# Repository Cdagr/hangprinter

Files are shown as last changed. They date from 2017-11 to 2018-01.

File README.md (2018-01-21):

Hangprinter Hangprinter logo
===========

This is the main dev branch of Megaprinter, based off Hangprinter v3.3.
Read [blog](http://vitana.se/opr3d/tbear) to stay up to date with what happens here.

Bill of Materials
----------------

  * Printed parts
    * Beam Clamp x 2
    * Beam Slider x 6
    * Corner Clamp x 3
    * Extruder Holder x 1
    * Lineroller ABC Winch x 3
    * Lineroller D x 3
    * Lineroller Anchor x 6 (The stl contains 2. Print <code>lineroller_anchor.stl</code> 3 times.)
    * Motor Bracket x 4
    * Motor Gear x 4
    * Spool x 4
    * Spool Gear x 4
    * Spacer x 4
    * Cable Clamp x ca 12
  * Vitamins
    * 5 x Nema17 steppers (> 40 N/cm holding torque, flat shaft)
    * 60 m FireLine 0.5 mm
    * ca 47x47 cm MDF or plywood sheet
    * 1 x Arduino Mega
    * 1 x RAMPS
    * 5 x drivers (Special configuration options exist if you use Mechaduinos or tmc2130SilentStepSticks)
    * 1 x USB cable, type B plug
    * 15x15 mm wooden beams (Tobben/core team uses lengths 3x40 cm + 1x20 cm)
    * 1 x Power supply (12 V, 10 A recommended)
    * 13 x M3 screws, length 25 mm
    * 16 x M3 screws, length 5 mm
    * 2  x M3 screws, length 10 mm
    * 4  x M8 screws, length > 50 mm, head countersunk
    * 8  x 608 bearing
    * 12 x 623 V-groove bearing
    * 10 cm PTFE tube (standard bowden, 4 mm outer dia, >1.75 mm inner dia)
    * More than 20 self tapping wooden screws, length 10 - 20 mm, width ca 4 mm
    * 5 m of 15-lead ribbon wire
    * Nuts and washers for all screws
    * Extruder + hot end (any setup that fits Nema17 mount will work)
    * Mechaduino optional addon
      * 4 x Mechaduino PCB
      * More than 20 jumper wires (if Mechaduinos)
      * 5V->3V3 level converter for i2c usage (if Mechaduinos)
    * Tmc2130SilentStepStick addon
      * A few more jumper wires

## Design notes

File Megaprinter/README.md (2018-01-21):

Hangprinter Hangprinter logo
===========

This is for a portable hangprinter tailored for exhibitions in large spaces.
Uses NEMA 23 stepper motors because of larger parts/higher inertia. Beefier motors helps avoid skipped steps w/ open loop control.
Designed in Fusion 360 because I'm not very good at openscad, but later things will be uploaded in openscad when things become more final.

Bill of Materials - Sorry, using hardware standard to US in early versions because they are easier for me to source. Metric to come!
----------------

  * Printed parts - Please print from ABS or other plastic with ~100C temperature resistance
    * Hopper/Fan Mount x 1
    * Bottle Mount x 1
  * Vitamins
    * 1 x NEMA23 stepper motor, 186 oz/in of greater
    * 1 x NEMA23 motor mounting bracket
    * 1 x 1/2in copper or aluminum pipe
    * 3 x 10-32 x 1.5in socket head cap screws
    * 3 x 4-40 x 1/8in set screws
    * 4 x 10-32 x 1/2in set screw
    * 3 x 10-32 x 1/2in countersunk screw
    * 4 x 8-32 x 3/4in socket head cap screws
    * 4 x 8-32 nylock nuts
    * 1/2in wood augur drill bit
    * 3 x heater cartridges, I use 24V 80W
    * 1 x motor coupler 1/4in to 5/16in
    * 1 x 40mm cooling fan, I use a server fan
  * Machined parts
    * Aluminum
      * Heat sink x 1
      * Heater block x 1
      * Nozzle(s) - lower cost than brass, ut brass can be used
      * Pipe mount x 1
      * Mounting plate x 1
      * #Optional# Pipe x1
    * Copper
      * Pipe x 1

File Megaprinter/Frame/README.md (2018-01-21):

Hangprinter Hangprinter logo
===========

These are the files for the frame of the megarinter.
The angles are weird because I threw the design together in a couple days without thinking much  about it.

Bill of Materials
----------------

  * Wood for the frame
    * 12ft 2x4 beams x 4
    * 16ft 2x4 beams x4
  * Plywood
    * Something in the ballpark of 3ftx3ft should be ok
  * Printed parts - Please print from ABS or other plastic with good impact resistance
    * Base joint x 3
    * Diagonal beam top joint mount x 3
  * Vitamins
    * 1 x NEMA23 stepper motor, 186 oz/in or greater
  * Sheet metal parts
    * Brace joint x 3
    * Center core joint x 1 #wait for new version#
    * Center base joint x 3 #wait for new version#

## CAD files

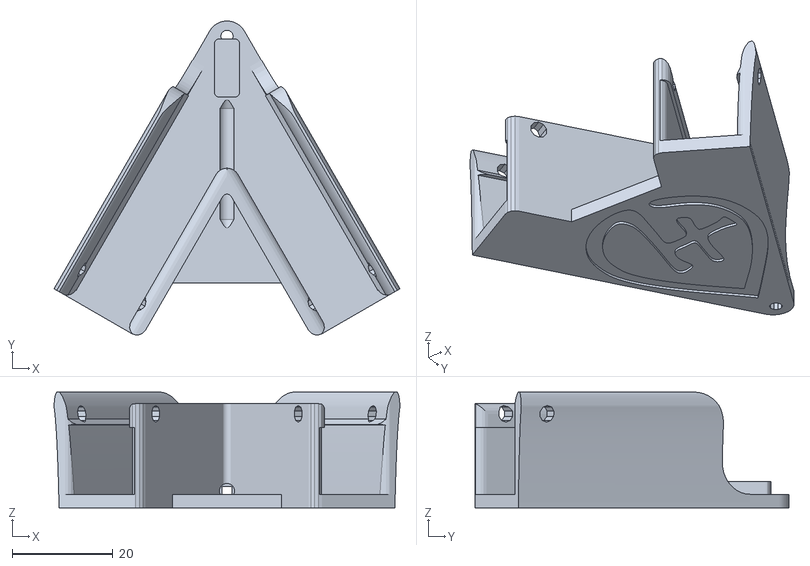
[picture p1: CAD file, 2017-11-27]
openscad_stl/corner_clamp_13mm.stl
68.6 x 62.2 x 22.9

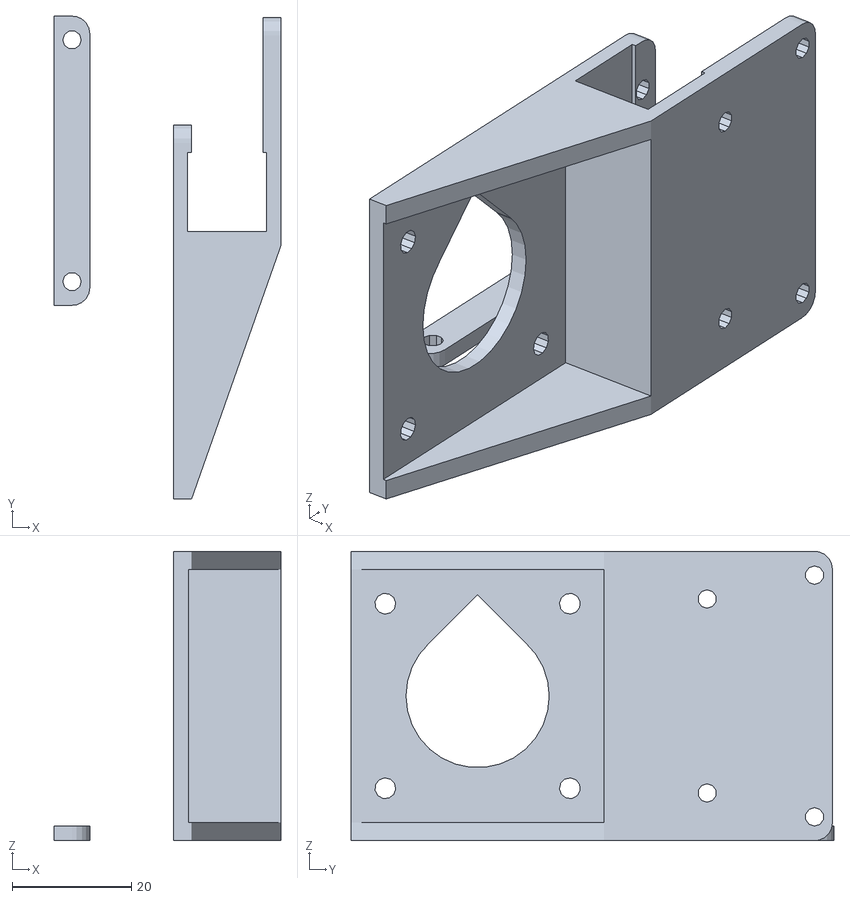
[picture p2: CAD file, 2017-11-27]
openscad_stl/extruder_holder_13mm.stl
38.0 x 80.9 x 48.5

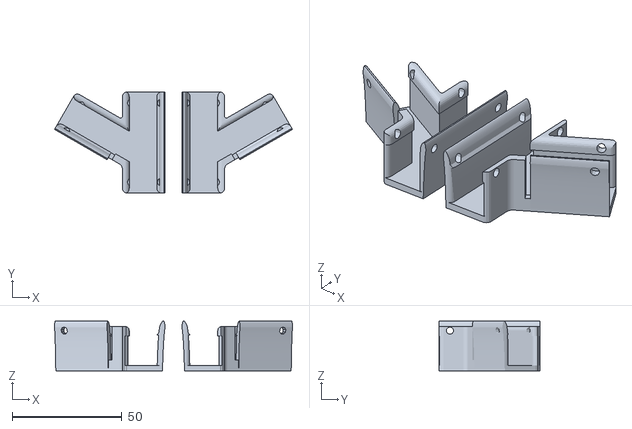
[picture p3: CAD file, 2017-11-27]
openscad_stl/beam_clamp_13mm.stl
108.3 x 46.0 x 22.6

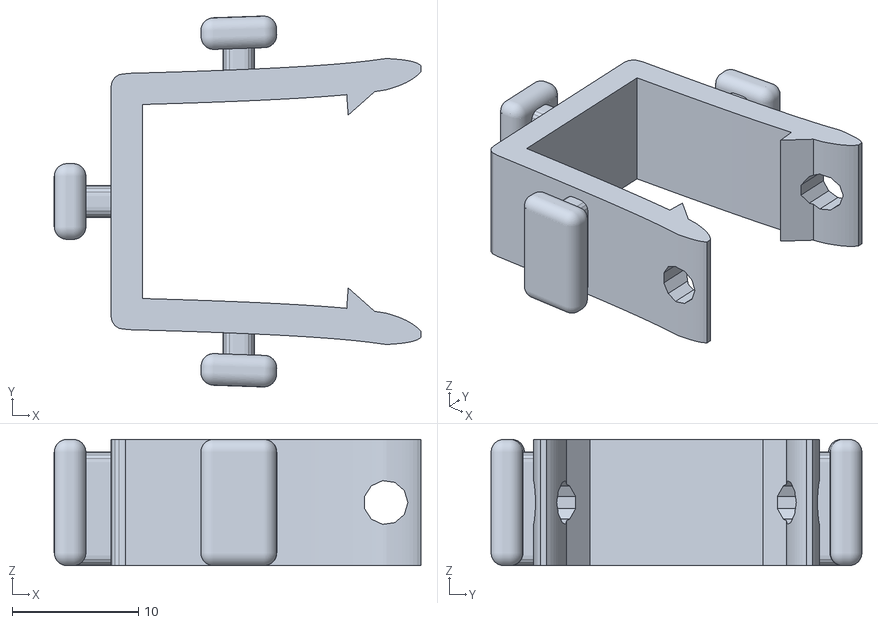
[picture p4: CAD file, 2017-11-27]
openscad_stl/beam_slider_15mm.stl
29.1 x 29.4 x 10.0

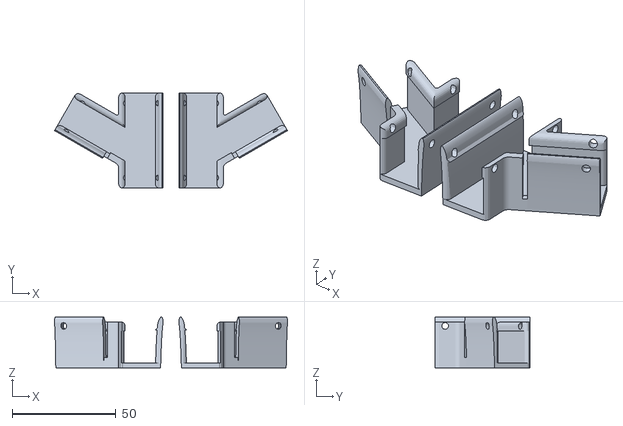
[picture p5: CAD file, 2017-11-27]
openscad_stl/beam_clamp_15mm.stl
112.3 x 46.0 x 24.6

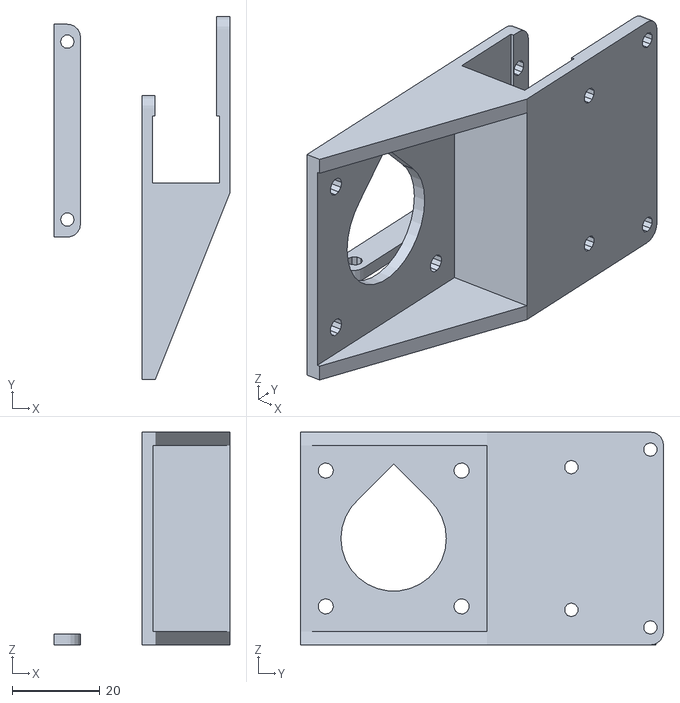
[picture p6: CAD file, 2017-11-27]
openscad_stl/extruder_holder_15mm.stl
40.0 x 82.7 x 48.5

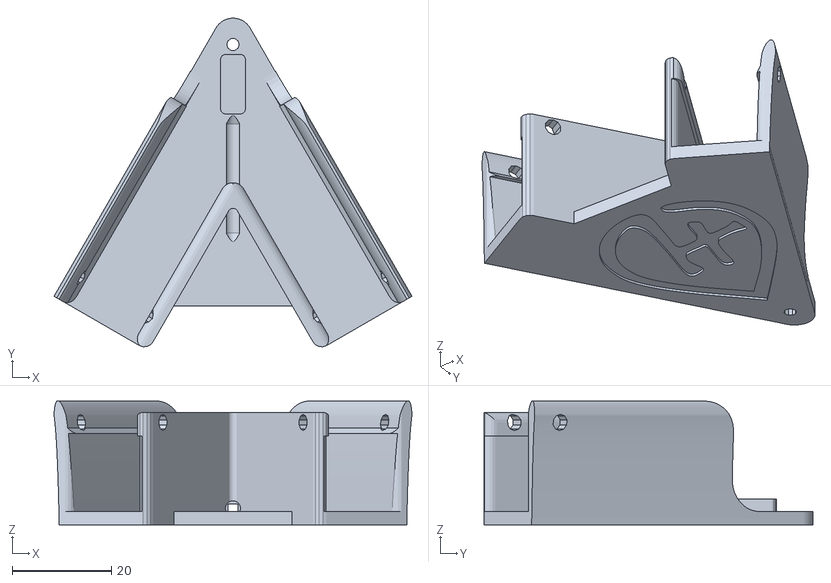
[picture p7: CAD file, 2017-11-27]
openscad_stl/corner_clamp_15mm.stl
72.1 x 66.2 x 24.9

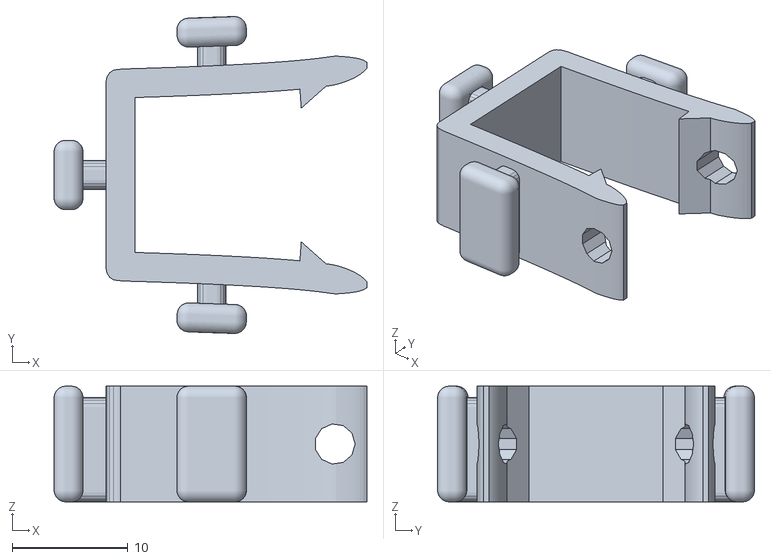
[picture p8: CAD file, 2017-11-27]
openscad_stl/beam_slider_13mm.stl
27.1 x 27.4 x 10.0

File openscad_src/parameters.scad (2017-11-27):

// Parameters shared between modules

Beam_width = 13;
Wiggle = 0.25;
Fat_beam_width = Beam_width + Wiggle;
Beam_length = 400;
Wall_th = 2.5;
Nema17_cube_width          = 42.43;
Nema17_screw_hole_width    = 43.74; // Opposite corner screws
Nema17_ring_diameter       = 22;
Nema17_cube_height         = 39.36;
Nema17_shaft_height        = 63.65;
Nema17_ring_height         = 2;
Nema17_screw_hole_width    = 43.74; // Opposite corner screws
Nema17_shaft_radius        = 5/2;

b608_outer_dia = 22.2;
b608_width = 7.05;

Gap_between_sandwich_and_plate = 1.7;

Clamp_wall_extra_length = 4.5;
Clamp_wall_flex_factor = 1.5;

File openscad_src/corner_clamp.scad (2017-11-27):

include <parameters.scad>
use <sweep.scad>
use <util.scad>

corner_clamp();
module corner_clamp(){
  wall_th = Wall_th+0.2; // A tad thicker since flex is very unwanted in this piece
  rad_b = 4;
  a = 13;
  b = Fat_beam_width+wall_th+2-a/2;
  l0 = 40;
  l1 = (Fat_beam_width+2*wall_th)*2*sqrt(3);
  edges = 0.625;
  opening_width = Fat_beam_width - 2*edges;
  d_hole_l = l0/2+2;

  difference(){
    union(){
      translate([-l1/2,-l1/sqrt(12),0])
      linear_extrude(height=wall_th)
        polygon(points = my_rounded_eqtri(l1,rad_b,5));
      difference(){
        for(k=[0,1])
          mirror([k,0,0])
            rotate([0,0,-30]){
              translate([-(Fat_beam_width+wall_th)+1, -l0+(wall_th+edges)*sqrt(3), 0]){
                one_rounded_cube4([Fat_beam_width+wall_th-1, l0+a-2, Fat_beam_width+2*wall_th+2],
                    2, $fn=4*4);
                translate([-wall_th-1,0,0])
                  cube([2*wall_th, l0+a, wall_th]);

               translate([Fat_beam_width/2-1, 0, Fat_beam_width/2+wall_th])
                 rotate([0,-90,-90])
                 clamp_wall(l0+a, lift_tri=1.0, w=Fat_beam_width+2*wall_th, wall_th=wall_th, edge=edges);

                }
              }

        extra_height_to_diff_of_clamp_wall = 2.30;
        for(k=[0,1])
          mirror([k,0,0])
        rotate([0,-90,30])
          translate([wall_th+a/2,(wall_th+edges)*sqrt(3)+a,-Fat_beam_width-2*wall_th-1]){
            cylinder(r=a/2, h=wall_th+edges+2, $fn=4*10);
            rotate([0,0,2*90])
            translate([-Fat_beam_width-wall_th-2-extra_height_to_diff_of_clamp_wall+a/2,+a/2,-1]){
              inner_round_corner(r=a/2, h=wall_th+edges+2,back=10, $fn=4*10);
              translate([extra_height_to_diff_of_clamp_wall,-b,0])
                cube([b,b, wall_th+edges+2+Clamp_wall_extra_length]);
            }
          }
      }
      translate([0,-sqrt(2)/sqrt(5),wall_th])
        rotate([0,0,-90-45])
        inner_round_corner(1,Fat_beam_width+wall_th+2,120,1.0, $fn=4*8);
    }
    scrw_fr_edg = 6;
    for(k=[0,1])
      mirror([k,0,0])
        rotate([0,0,-30]){
          translate([-Fat_beam_width-wall_th, -l0+4, wall_th]){
            cube([Fat_beam_width, l0+a+2, Fat_beam_width]);
          }
          translate([-opening_width-wall_th-edges, -l0+4, wall_th]){
            cube([opening_width, l0+a+2, Fat_beam_width+20]);
            translate([-wall_th-edges,0,-wall_th]){
              opening_top(exclude_left = true, wall_th=wall_th, edges=edges, l=l0+2);
              translate([-0.0,wall_th-1,0])
              opening_corners(left_one_height=2*Fat_beam_width, wall_th=wall_th, edges=edges);
            }

          }
          translate([0,0,Fat_beam_width+2*wall_th+2-2])
            rotate([0,-90,0])
              translate([0,-l0+(wall_th+edges)*sqrt(3)+scrw_fr_edg,-2])
                cylinder(d=3.3, h=Fat_beam_width+2*wall_th+4, $fn=10);

        }
    translate([0,l0-3*Beam_width/4,-1])
      cylinder(d=2.5, h=wall_th+6, $fn=10);


    translate([0,0,-0.5])
    linear_extrude(height=1)
      scale(0.15)
      mirror([1,0])
      translate([-150.3,-114])
      import("logo.dxf");

    d_hole_r = 1.5;
    translate([0,-6,2+wall_th/2])
      rotate([-90,0,0]){
        translate([0,0,d_hole_l-0.01])
            rotate([0,0,45])
          cylinder(r1=d_hole_r+0.01, r2=0.5, h=2,$fn=40);
            rotate([0,0,45])
        cylinder(r=d_hole_r, h=d_hole_l,$fn=40);
        translate([0,0,-2+0.01])
            rotate([0,0,45])
          cylinder(r2=d_hole_r+0.01, r1=0.5, h=2,$fn=40);
      }
    fillet_r = 2.5;
    translate([0,(wall_th+edges-fillet_r)*2,0]){
      rotate([0,0,-90-45])
        translate([-fillet_r, -fillet_r,wall_th])
          translate([fillet_r*(1-cos(15)),fillet_r*(1-cos(15)),0])
            inner_round_corner(fillet_r,30,120,2, $fn=4*8);
    }


  }

  // Channel to guide D-line and stiffen up corner

  channel_l = ((l0-3*Beam_width/4)+(d_hole_l-6))/4;
  channel_r1 = 1;
  channel_r2 = 2.5;
  translate([0,((l0-2*rad_b)+(d_hole_l-6))/2,wall_th])
    rotate([90,0,0])
        difference(){
          rotate([90,0,0])
            translate([-channel_r2, -channel_l/2, -channel_r2])
              rounded_cube2([2*channel_r2, channel_l, channel_r2+0.1], 1, $fn=4*4);
          rotate([90,0,0])
            translate([-channel_r1, -channel_l/2-1, -channel_r1-0.5])
             cube([2*channel_r1, channel_l+2, 2*channel_r1]);
        }
}

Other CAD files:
Megaprinter/Frame/Frame.f3d
Megaprinter/Pellet Extruder/Extruder Hotend Combo.f3d

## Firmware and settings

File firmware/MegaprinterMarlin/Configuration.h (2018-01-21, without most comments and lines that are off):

#define CONFIGURATION_H
#include "boards.h"
#define STRING_VERSION "3.3.hangprinter"
#define STRING_URL "github.com/tobbelobb/hangprinter"
#define STRING_VERSION_CONFIG_H __DATE__ " " __TIME__ // build date and time
#define STRING_CONFIG_H_AUTHOR "tobbelobb w/ modifications by Chris Dagher" // Who made the changes.
#define STRING_SPLASH_LINE1 "v" STRING_VERSION // will be shown during bootup in line 1
#define SERIAL_PORT 0
#define BAUDRATE 250000
#define MOTHERBOARD BOARD_RAMPS_13_EEF
#define CUSTOM_MENDEL_NAME "MEGAPRINTER"
#define EXTRUDERS 1
#define POWER_SUPPLY 1
#define DELTA
#define HANGPRINTER
#define DELTA_SEGMENTS_PER_SECOND 40
#define ANCHOR_A_X 0.0
#define ANCHOR_A_Y -2163.0
#define ANCHOR_A_Z -75.5
#define ANCHOR_B_X -1841.0
#define ANCHOR_B_Y 741.0
#define ANCHOR_B_Z -75.5
#define ANCHOR_C_X 1639.0
#define ANCHOR_C_Y 1404.0
#define ANCHOR_C_Z -75.5
#define ANCHOR_D_Z 3250.5
#define NUM_AXIS 5 // The axis order: A_AXIS, B_AXIS, C_AXIS, D_AXIS, E_AXIS
#define DIRS 4
#define EXPERIMENTAL_LINE_BUILDUP_COMPENSATION_FEATURE
#define MECHANICAL_ADVANTAGE_A 1
#define MECHANICAL_ADVANTAGE_B 1
#define MECHANICAL_ADVANTAGE_C 1
#define MECHANICAL_ADVANTAGE_D 1
#define ACTION_POINTS_A 2
#define ACTION_POINTS_B 2
#define ACTION_POINTS_C 2
#define ACTION_POINTS_D 3
const int nr_of_lines_in_direction[DIRS] = {MECHANICAL_ADVANTAGE_A*ACTION_POINTS_A,
                                            MECHANICAL_ADVANTAGE_B*ACTION_POINTS_B,
                                            MECHANICAL_ADVANTAGE_C*ACTION_POINTS_C,
                                            MECHANICAL_ADVANTAGE_D*ACTION_POINTS_D};
#define DEFAULT_SPOOL_BUILDUP_FACTOR 0.005093
const float MOUNTED_LINE[DIRS] = {7500.0,7500.0,7500.0,7500.0};
const float SPOOL_RADII[DIRS] = { 97.5, 97.5, 97.5, 97.5 };
const float STEPS_PER_SPOOL_RADIAN[DIRS] = {5093.0, 5093.0, 5093.0, 5093.0};
#define TEMP_SENSOR_0 1 // Setting gotten from thermistor manufacturer
#define TEMP_SENSOR_1 0
#define TEMP_SENSOR_2 0
#define TEMP_RESIDENCY_TIME 10  // (seconds)
#define TEMP_HYSTERESIS 3       // (degC) range of +/- temperatures considered "close" to the target one
#define TEMP_WINDOW     1       // (degC) Window around target to start the residency timer x degC early.
#define HEATER_0_MINTEMP 10
#define HEATER_1_MINTEMP  0
#define HEATER_2_MINTEMP  0
#define HEATER_0_MAXTEMP 260
#define HEATER_1_MAXTEMP 260
#define HEATER_2_MAXTEMP 260
#define PIDTEMP
#define BANG_MAX 127 // limits current to nozzle while in bang-bang mode; 255=full current
#define PID_MAX 127 // limits current to nozzle while PID is active (see PID_FUNCTIONAL_RANGE below); 255=full current
#define PID_FUNCTIONAL_RANGE 20 // If the temperature difference between the target temperature and the actual temperature
#define PID_INTEGRAL_DRIVE_MAX 255  //limit for the integral term
#define K1 0.95 //smoothing factor within the PID
#define PID_dT ((OVERSAMPLENR * 10.0)/(F_CPU / 64.0 / 256.0)) //sampling period of the temperature routine
#define  DEFAULT_Kp 39.76
#define  DEFAULT_Ki 5
#define  DEFAULT_Kd 125
#define PREVENT_DANGEROUS_EXTRUDE
#define EXTRUDE_MINTEMP 170
#define EXTRUDE_MAXLENGTH (X_MAX_LENGTH+Y_MAX_LENGTH) //prevent extrusion of very large distances.
#define THERMAL_RUNAWAY_PROTECTION_PERIOD 60 //in seconds
#define THERMAL_RUNAWAY_PROTECTION_HYSTERESIS 10 // in degree Celsius
#define ENDSTOPPULLUPS // Comment this out (using // at the start of the line) to disable the endstop pullup resistors
#define ENDSTOPPULLUP_XMAX
#define ENDSTOPPULLUP_YMAX
#define ENDSTOPPULLUP_ZMAX
#define ENDSTOPPULLUP_XMIN
#define ENDSTOPPULLUP_YMIN
#define ENDSTOPPULLUP_ZMIN
const bool X_MIN_ENDSTOP_INVERTING = true; // set to true to invert the logic of the endstop.
const bool Y_MIN_ENDSTOP_INVERTING = true; // set to true to invert the logic of the endstop.
const bool Z_MIN_ENDSTOP_INVERTING = true; // set to true to invert the logic of the endstop.
const bool X_MAX_ENDSTOP_INVERTING = true; // set to true to invert the logic of the endstop.
const bool Y_MAX_ENDSTOP_INVERTING = true; // set to true to invert the logic of the endstop.
const bool Z_MAX_ENDSTOP_INVERTING = true; // set to true to invert the logic of the endstop.
#define DISABLE_MIN_ENDSTOPS
#define X_ENABLE_ON 0
#define Y_ENABLE_ON 0
#define Z_ENABLE_ON 0
#define E_ENABLE_ON 0 // For all extruders
#define DISABLE_X false
#define DISABLE_Y false
#define DISABLE_Z false
#define DISABLE_E false // For all extruders
#define DISABLE_INACTIVE_EXTRUDER false //disable only inactive extruders and keep active extruder enabled
#define INVERT_X_DIR false // INVERT_A
#define INVERT_Y_DIR true  // INVERT_B
#define INVERT_Z_DIR false // INVERT_C
#define INVERT_E0_DIR false   // INVERT_E
#define INVERT_E1_DIR true    // INVERT_D
#define INVERT_E2_DIR false
#define X_HOME_DIR 1
#define Y_HOME_DIR 1
#define Z_HOME_DIR 1
#define min_software_endstops false // If true, axis won't move to coordinates less than HOME_POS.
#define max_software_endstops false  // If true, axis won't move to coordinates greater than the defined lengths below.
#define X_MAX_POS 90
#define X_MIN_POS -90
#define Y_MAX_POS 90
#define Y_MIN_POS -90
#define Z_MAX_POS MANUAL_Z_HOME_POS
#define Z_MIN_POS 0
#define A_MAX_POS 900
#define A_MIN_POS -900
#define B_MAX_POS 900
#define B_MIN_POS -900
#define C_MAX_POS 900
#define C_MIN_POS -900
#define D_MAX_POS MANUAL_Z_HOME_POS
#define D_MIN_POS 0
#define X_MAX_LENGTH (X_MAX_POS - X_MIN_POS)
#define Y_MAX_LENGTH (Y_MAX_POS - Y_MIN_POS)
#define Z_MAX_LENGTH (Z_MAX_POS - Z_MIN_POS)
#define MANUAL_HOME_POSITIONS  // MANUAL_*_HOME_POS below will be used
#define MANUAL_X_HOME_POS 0
#define MANUAL_Y_HOME_POS 0
#define MANUAL_Z_HOME_POS 0
#define HOMING_FEEDRATE {200*60, 200*60, 200*60, 200*60, 0}  // set the homing speeds (mm/min)
#define DEFAULT_ESTEPS 70 // 1/8 ustep @ 200 steps/rev with auger
#define DEFAULT_AXIS_STEPS_PER_UNIT   {0, 0, 0, 0, DEFAULT_ESTEPS}
#define DEFAULT_MAX_FEEDRATE          {500, 500, 500, 300, 25}    // (mm/sec)
#define DEFAULT_MAX_ACCELERATION      {2000,2000,2000,2000,10000}    // X, Y, Z, E maximum start speed for accelerated moves.
#define DEFAULT_ACCELERATION          1000    // X, Y, Z and E max acceleration in mm/s^2 for printing moves
#define DEFAULT_RETRACT_ACCELERATION  3000   // X, Y, Z and E max acceleration in mm/s^2 for retracts
#define DEFAULT_NOMINAL_FILAMENT_DIA 1.75
#define DEFAULT_XYJERK                13.0    // (mm/sec)
#define DEFAULT_ZJERK                 13.0    // (mm/sec)
#define DEFAULT_EJERK                 5.0    // (mm/sec)
#define EEPROM_SETTINGS
#define EEPROM_CHITCHAT
#define PLA_PREHEAT_HOTEND_TEMP 180
#define PLA_PREHEAT_HPB_TEMP 0
#define PLA_PREHEAT_FAN_SPEED 255   // Insert Value between 0 and 255
#define SOFT_PWM_SCALE 0
#include "Configuration_adv.h"
#include "thermistortables.h"

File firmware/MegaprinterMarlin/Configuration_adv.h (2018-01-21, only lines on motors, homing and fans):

#define CONTROLLERFAN_PIN -1 //Pin used for the fan to cool controller (-1 to disable)
#define EXTRUDER_0_AUTO_FAN_PIN    8
#define EXTRUDER_1_AUTO_FAN_PIN   -1
#define EXTRUDER_2_AUTO_FAN_PIN   -1
#define ENDSTOPS_ONLY_FOR_HOMING // If defined the endstops will only be used for homing
#define X_HOME_POS MANUAL_X_HOME_POS
#define Y_HOME_POS MANUAL_Y_HOME_POS
#define Z_HOME_POS MANUAL_Z_HOME_POS
#define X_HOME_RETRACT_MM 5
#define Y_HOME_RETRACT_MM 5
#define Z_HOME_RETRACT_MM 5 // deltas need the same for all three axis
#define MICROSTEP1 LOW,LOW
#define MICROSTEP2 HIGH,LOW
#define MICROSTEP4 LOW,HIGH
#define MICROSTEP8 HIGH,HIGH
#define MICROSTEP16 HIGH,HIGH
#define MICROSTEP_MODES {16,16,16,16,16} // [1,2,4,8,16]
#define DIGIPOT_MOTOR_CURRENT {135,135,135,135,135} // Values 0-255 (RAMBO 135 = ~0.75A, 185 = ~1A)
#define DIGIPOT_I2C_MOTOR_CURRENTS {1.0, 1.0, 1.0, 1.0, 1.0, 1.0, 1.0, 1.0}

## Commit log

2017-11-27 Creates 13 mm versions of parts that depend on Beam_width
    [beam_clamp_13mm.stl, beam_clamp_15mm.stl, beam_slider_13mm.stl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]
2018-01-20 Initial commit
    High powered custom toolhead combining hotend and extruder. Inspired by design of my old Filastruder
    [Extruder Hotend Combo.f3d]
2018-01-21 Initial commit
    Creates folder for files and adds pellet extruder
    [Extruder Hotend Combo.f3d]
2018-01-21 Add frame file
    Bad design, I highly recommend not using it until I clean it up a bit.
    [Frame.f3d]
2018-01-21 Add megaprinter marlin
    [Configuration.h, Configuration_adv.h]
